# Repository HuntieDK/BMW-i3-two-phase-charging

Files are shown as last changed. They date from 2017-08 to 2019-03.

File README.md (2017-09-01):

# BMW i3 60Ah two-phase charging

This repository contains schematics, PCB layout and Arduino IDE compatible
code for extending the BMW i3 60Ah BEV/REX charging to use two phases
for charging through the type 2 receptable in the car.

## Background

The BMW i3 60Ah is designed to charge with 230V/32A (7.4kW) from a single
phase supply. However often a three-phase 230V/16A supply is available
which can supply 11kW, but this only lets the i3 charge with 230V/16A (3.7kW),
as the i3 can only use one of the phases.

Internally in the car, the 32A current is split between two charging units,
the EME and the KLE. These actually pull up to 16A each, and can, with
modification, be made to charge from two individual phases. In this way,
the car can charge from two phases, 230V at 16A each, in total 7.4kW.

## Implementation

* The wiring in the car must be changed. A new three-phase socket must be
  installed and new wiring must be pulled from the replaced socket to the
  KLE and EME units

* The car must be persuaded to pull what it believes is 32A in order to
  pull 16A on each phase. That is accomplished by the electronics and
  firmware in this repository. It must be inserted in the proximity and
  control pilot signals between the car's charging socket and the charging
  controller, LIM. The main function of the circuit is to signal "32A" over
  the control pilot line whenever the connected EVSE signals "16A" or more.

## Warning

This modification of the BMW i3 60Ah IS NOT SIMPLE! It requires electrical,
mecanical and electronical skills to complete the modification succesfully
in a safe way. The information here is provided "as is" without warranty of
any kind. See attached license.

ANY WORK YOU PERFORM BASED ON THIS DESCRIPTION IS YOUR OWN RESPONSIBILITY!

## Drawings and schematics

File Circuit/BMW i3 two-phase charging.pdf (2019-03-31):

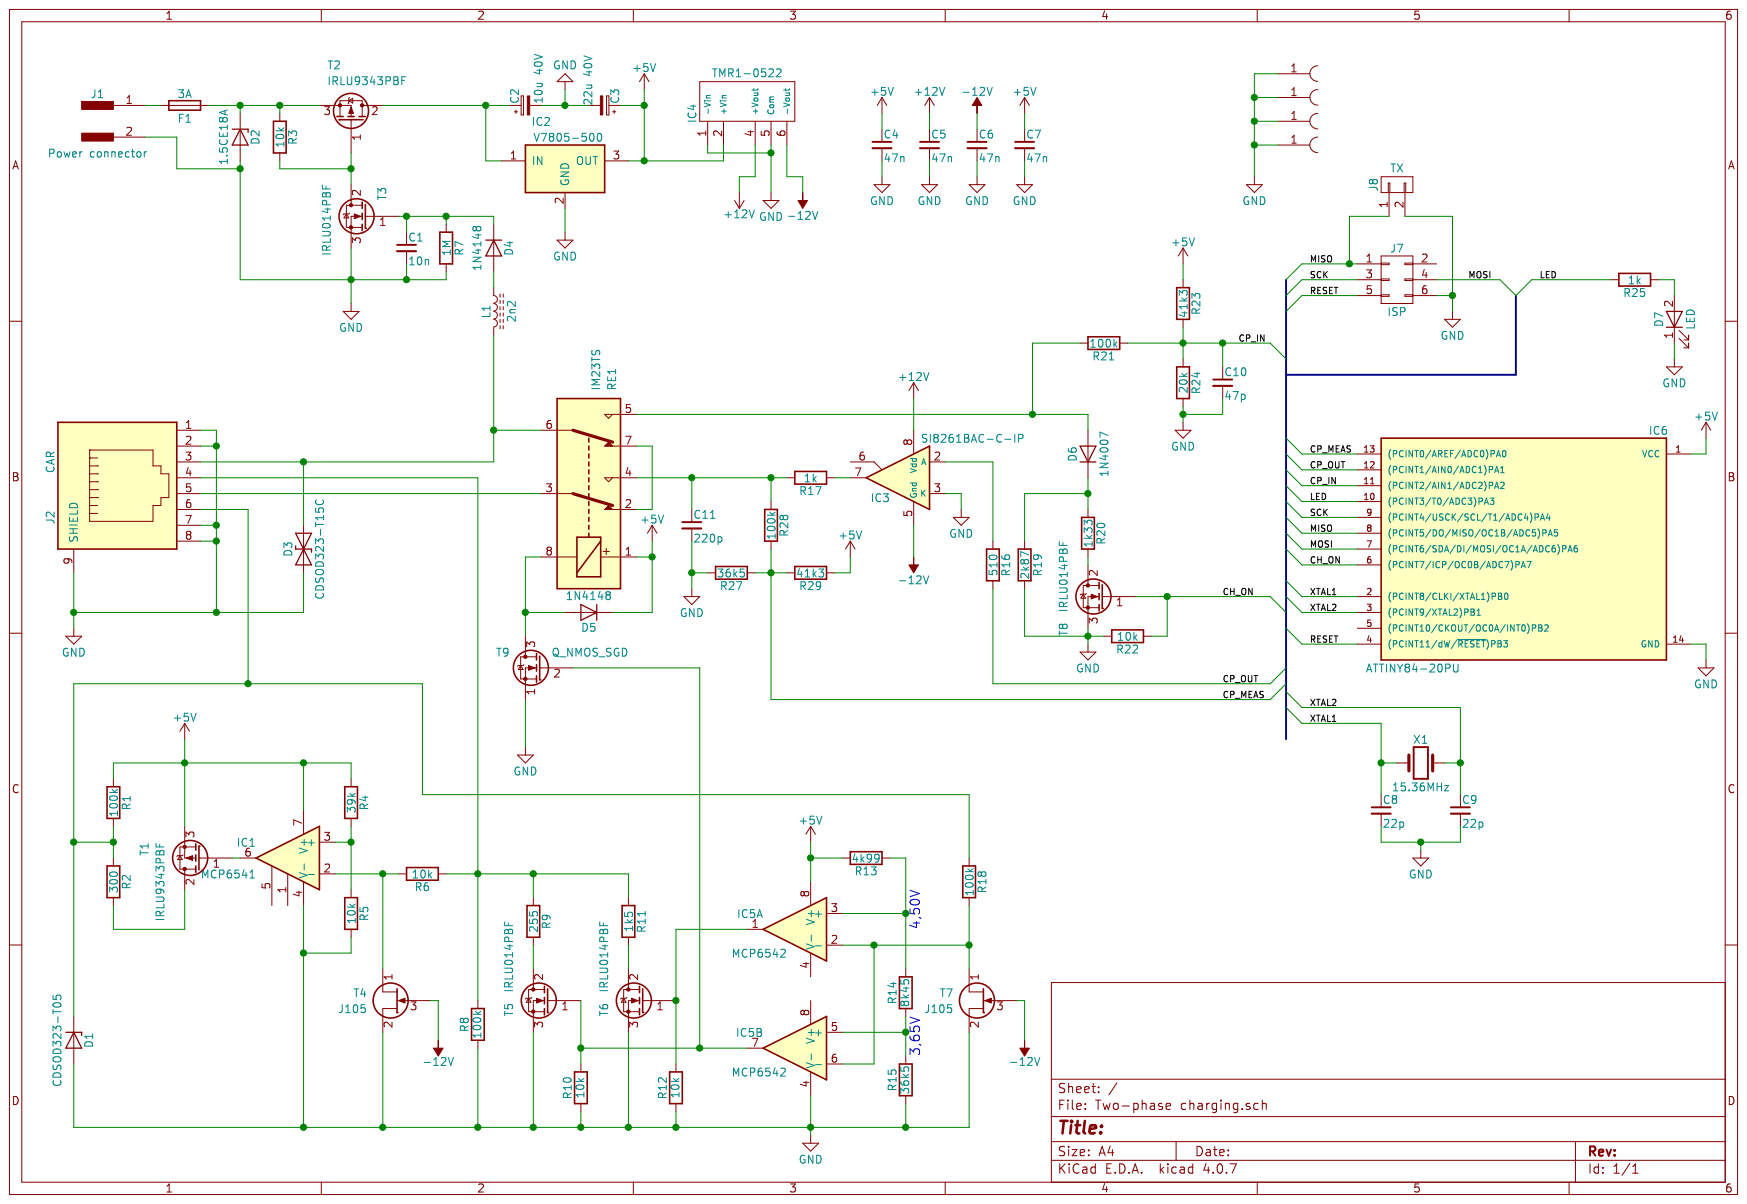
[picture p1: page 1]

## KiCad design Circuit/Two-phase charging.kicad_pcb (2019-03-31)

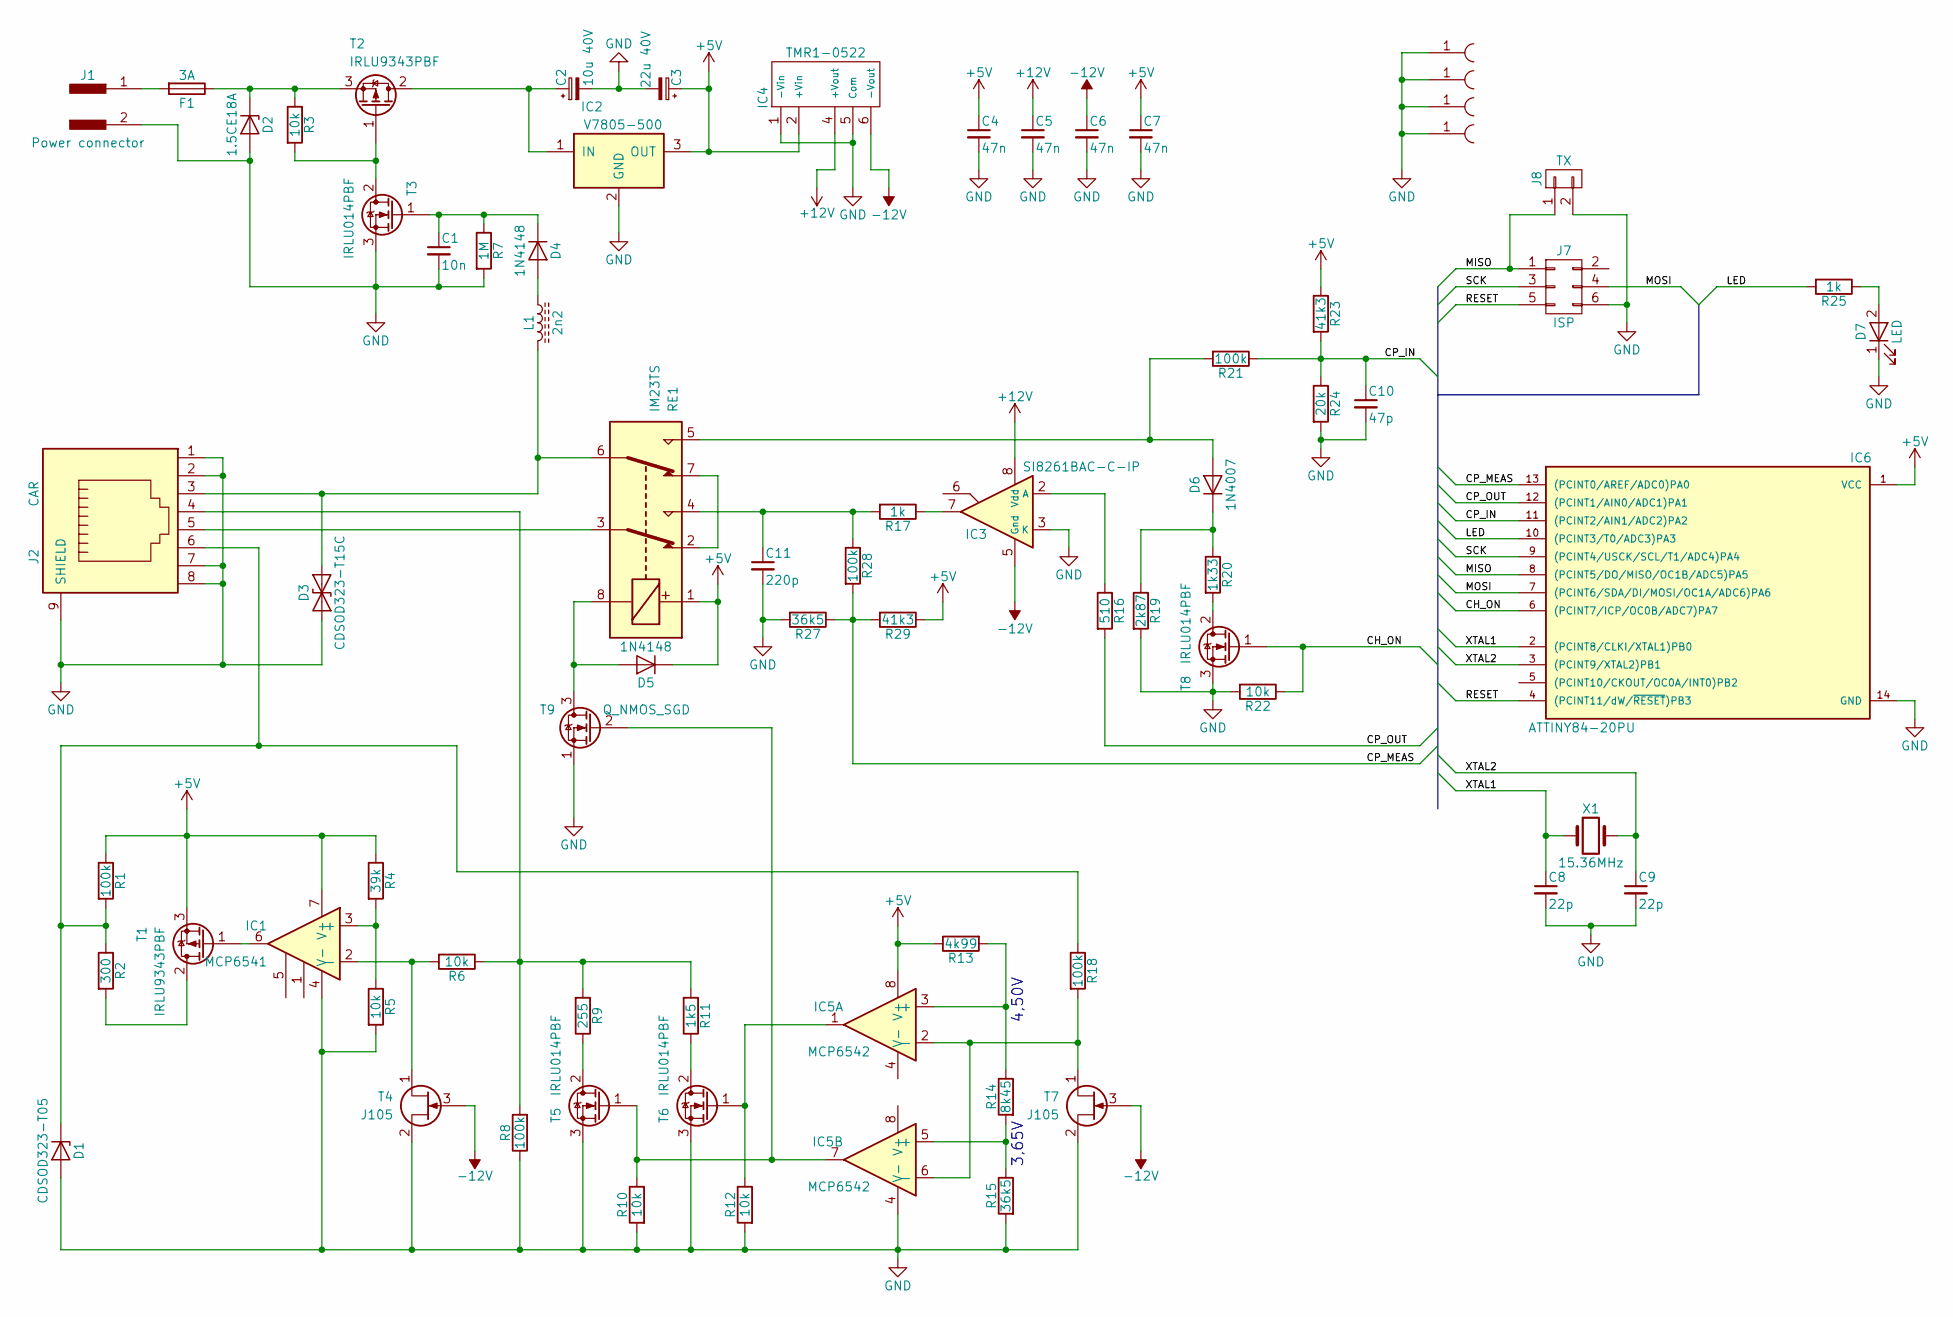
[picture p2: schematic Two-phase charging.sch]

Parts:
C1: 10n; C_Disc_D5.1mm_W3.2mm_P5.08mm
C2: 10u 40V; CP_Radial_D5.0mm_P2.50mm
C3: 22u 40V; CP_Radial_D5.0mm_P2.50mm
C4, C5, C6, C7: 47n; C_Disc_D5.1mm_W3.2mm_P5.08mm
C8, C9: 22p; Pin_Header_Straight_1x02_Pitch2.54mm
C10: 47p; Pin_Header_Straight_1x02_Pitch2.54mm
C11: 220p; Pin_Header_Straight_1x02_Pitch2.54mm
D1: CDSOD323-T05; D_SOD-323_HandSoldering
D2: 1.5CE18A; D_DO-201AD_P12.70mm_Horizontal
D3: CDSOD323-T15C; D_SOD-323_HandSoldering
D4, D5: 1N4148; D_DO-41_SOD81_P7.62mm_Horizontal
D6: 1N4007; D_DO-41_SOD81_P10.16mm_Horizontal
D7: LED; LED_D3.0mm
F1: 3A; R_Axial_DIN0207_L6.3mm_D2.5mm_P10.16mm_Horizontal
IC1: MCP6541; DIP-8_W7.62mm_LongPads
IC2: V7805-500; VX78xx-500
IC3: SI8261BAC-C-IP; DIP-8_W7.62mm_LongPads
IC4: TMR1-0522; Recom_1x05_Pitch2.54mm
IC5: MCP6542; DIP-8_W7.62mm_LongPads
IC6: ATTINY84-20PU; DIP-14_W7.62mm_LongPads
J1: Power connector; PINHEAD1-2
J2: CAR; RJ45_8_TM21R
J3, J4, J5, J6: Mount; MountingHole_3.5mm_Pad
J7: ISP; Pin_Header_Straight_2x03_Pitch2.54mm
J8: TX; Pin_Header_Straight_1x02_Pitch2.54mm
L1: 2n2; L_Axial_L11.0mm_D4.5mm_P5.08mm_Vertical_Fastron_MECC
R1, R8, R18, R21, R28: 100k; R_Axial_DIN0207_L6.3mm_D2.5mm_P10.16mm_Horizontal
R2: 300; R_Axial_DIN0207_L6.3mm_D2.5mm_P10.16mm_Horizontal
R3, R5, R6, R10, R12, R22: 10k; R_Axial_DIN0207_L6.3mm_D2.5mm_P10.16mm_Horizontal
R4: 39k; R_Axial_DIN0207_L6.3mm_D2.5mm_P10.16mm_Horizontal
R7: 1M; R_Axial_DIN0207_L6.3mm_D2.5mm_P10.16mm_Horizontal
R9: 255; R_Axial_DIN0207_L6.3mm_D2.5mm_P10.16mm_Horizontal
R11: 1k5; R_Axial_DIN0207_L6.3mm_D2.5mm_P10.16mm_Horizontal
R13: 4k99; R_Axial_DIN0207_L6.3mm_D2.5mm_P10.16mm_Horizontal
R14: 8k45; R_Axial_DIN0207_L6.3mm_D2.5mm_P10.16mm_Horizontal
R15, R27: 36k5; R_Axial_DIN0207_L6.3mm_D2.5mm_P10.16mm_Horizontal
R16: 510; R_Axial_DIN0207_L6.3mm_D2.5mm_P10.16mm_Horizontal
R17, R25: 1k; R_Axial_DIN0207_L6.3mm_D2.5mm_P10.16mm_Horizontal
R19: 2k87; R_Axial_DIN0207_L6.3mm_D2.5mm_P10.16mm_Horizontal
R20: 1k33; R_Axial_DIN0207_L6.3mm_D2.5mm_P10.16mm_Horizontal
R23, R29: 41k3; R_Axial_DIN0207_L6.3mm_D2.5mm_P10.16mm_Horizontal
R24: 20k; R_Axial_DIN0207_L6.3mm_D2.5mm_P10.16mm_Horizontal
RE1: IM23TS; Relay_DPDT_AXICOM_IMSeries_Pitch5.08mm
T1, T2: IRLU9343PBF; TO-251_IPAK_Vertical
T3, T5, T6, T8: IRLU014PBF; TO-251_IPAK_Vertical
T4, T7: J105; TO-92_Molded_Wide
T9: Q_NMOS_SGD; TO-92_Molded_Wide
X1: 15.36MHz; Crystal_HC49-U_Vertical

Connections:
+5V: C3.1, C4.1, C7.1, D5.1 (K), IC1.7 (V+), IC2.3 (OUT), IC4.2 (+Vin), IC5.8 (V+), IC6.1 (VCC), R1.1, R4.1, R13.1, R23.1, R29.1, RE1.1, T1.3 (S)
+12V: C5.1, IC3.8 (Vdd), IC4.4 (+Vout)
-12V: C6.1, IC3.5 (Gnd), IC4.6 (-Vout), T4.3 (G), T7.3 (G)
/CH_ON: IC6.6 ((PCINT7/ICP/OC0B/ADC7)PA7), R22.1, T8.1 (G)
/CP_IN: C10.1, IC6.11 ((PCINT2/AIN1/ADC2)PA2), R21.1, R23.2, R24.1
/CP_MEAS: IC6.13 ((PCINT0/AREF/ADC0)PA0), R27.1, R28.2, R29.2
/CP_OUT: IC6.12 ((PCINT1/AIN0/ADC1)PA1), R16.2
/LED: IC6.10 ((PCINT3/T0/ADC3)PA3), R25.2
/MISO: IC6.8 ((PCINT5/DO/MISO/OC1B/ADC5)PA5), J7.1, J8.1
/MOSI: IC6.7 ((PCINT6/SDA/DI/MOSI/OC1A/ADC6)PA6), J7.4
/RESET: IC6.4 ((PCINT11/dW/~RESET~)PB3), J7.5
/SCK: IC6.9 ((PCINT4/USCK/SCL/T1/ADC4)PA4), J7.3
/XTAL1: C8.1, IC6.2 ((PCINT8/CLKI/XTAL1)PB0), X1.1
/XTAL2: C9.1, IC6.3 ((PCINT9/XTAL2)PB1), X1.2
GND: C1.2, C2.2, C3.2, C4.2, C5.2, C6.2, C7.2, C8.2, C9.2, C10.2, C11.2, D1.2 (A), D2.2 (A), D3.1 (A1), D7.1 (K), IC1.4 (V-), IC2.2 (GND), IC3.3 (K), IC4.1 (-Vin), IC4.5 (Com), IC5.4 (V-), IC6.14 (GND), J1.2, J2.1, J2.2, J2.7, J2.8, J2.9 (SHIELD), J3.1, J4.1, J5.1, J6.1, J7.6, J8.2, R5.2, R7.2, R8.1, R10.2, R12.2, R15.2, R19.2, R22.2, R24.2, R27.2, T3.3 (S), T4.2 (S), T5.3 (S), T6.3 (S), T7.2 (S), T8.3 (S), T9.1 (S)
unnamed: C1.1, D4.1 (K), R7.1, T3.1 (G)
unnamed: C2.1, IC2.1 (IN), T2.2 (D)
unnamed: C11.1, R17.2, R28.1, RE1.4
unnamed: D1.1 (K), J2.6, R1.2, R2.1, R18.1
unnamed: D2.1 (K), F1.1, R3.1, T2.3 (S)
unnamed: D3.2 (A2), J2.3, L1.2, RE1.6
unnamed: D4.2 (A), L1.1
unnamed: D5.2 (A), RE1.8, T9.3 (D)
unnamed: D6.1 (K), R19.1, R20.1
unnamed: D6.2 (A), R21.2, RE1.5
unnamed: D7.2 (A), R25.1
unnamed: F1.2, J1.1
unnamed: IC1.2 (-), R6.2, T4.1 (D)
unnamed: IC1.3 (+), R4.2, R5.1
unnamed: IC1.6, T1.1 (G)
unnamed: IC3.2 (A), R16.1
unnamed: IC3.7, R17.1
unnamed: IC5.1, R12.1, T6.1 (G)
unnamed: IC5.2 (-), IC5.6 (-), R18.2, T7.1 (D)
unnamed: IC5.3 (+), R13.2, R14.1
unnamed: IC5.5 (+), R14.2, R15.1
unnamed: IC5.7, R10.1, T5.1 (G), T9.2 (G)
unnamed: J2.4, R6.1, R8.2, R9.2, R11.2
unnamed: J2.5, RE1.3
unnamed: R2.2, T1.2 (D)
unnamed: R3.2, T2.1 (G), T3.2 (D)
unnamed: R9.1, T5.2 (D)
unnamed: R11.1, T6.2 (D)
unnamed: R20.2, T8.2 (D)
unnamed: RE1.2, RE1.7

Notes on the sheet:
3,65V
4,50V

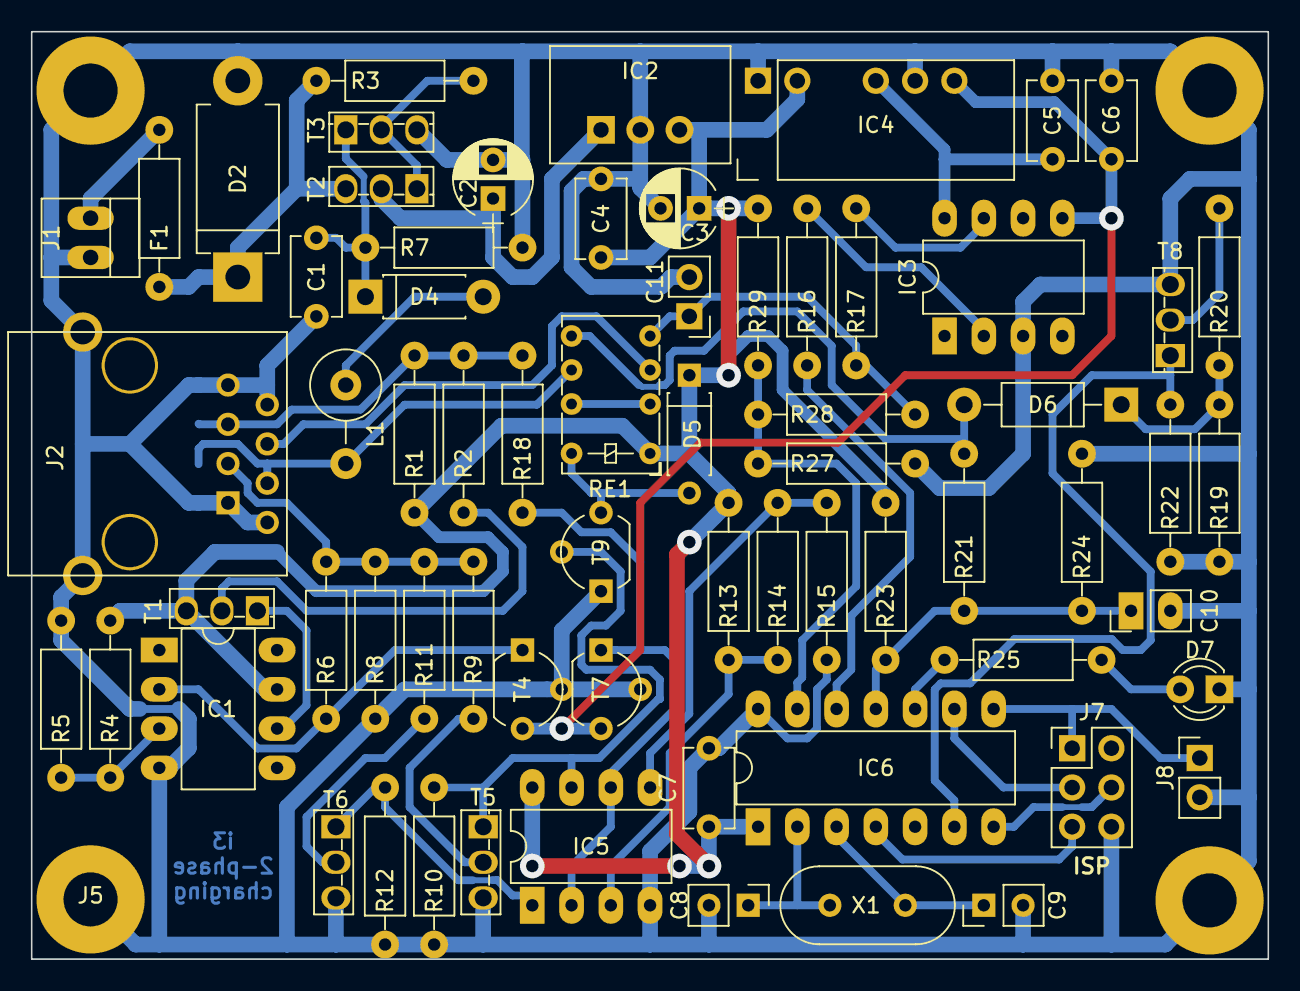
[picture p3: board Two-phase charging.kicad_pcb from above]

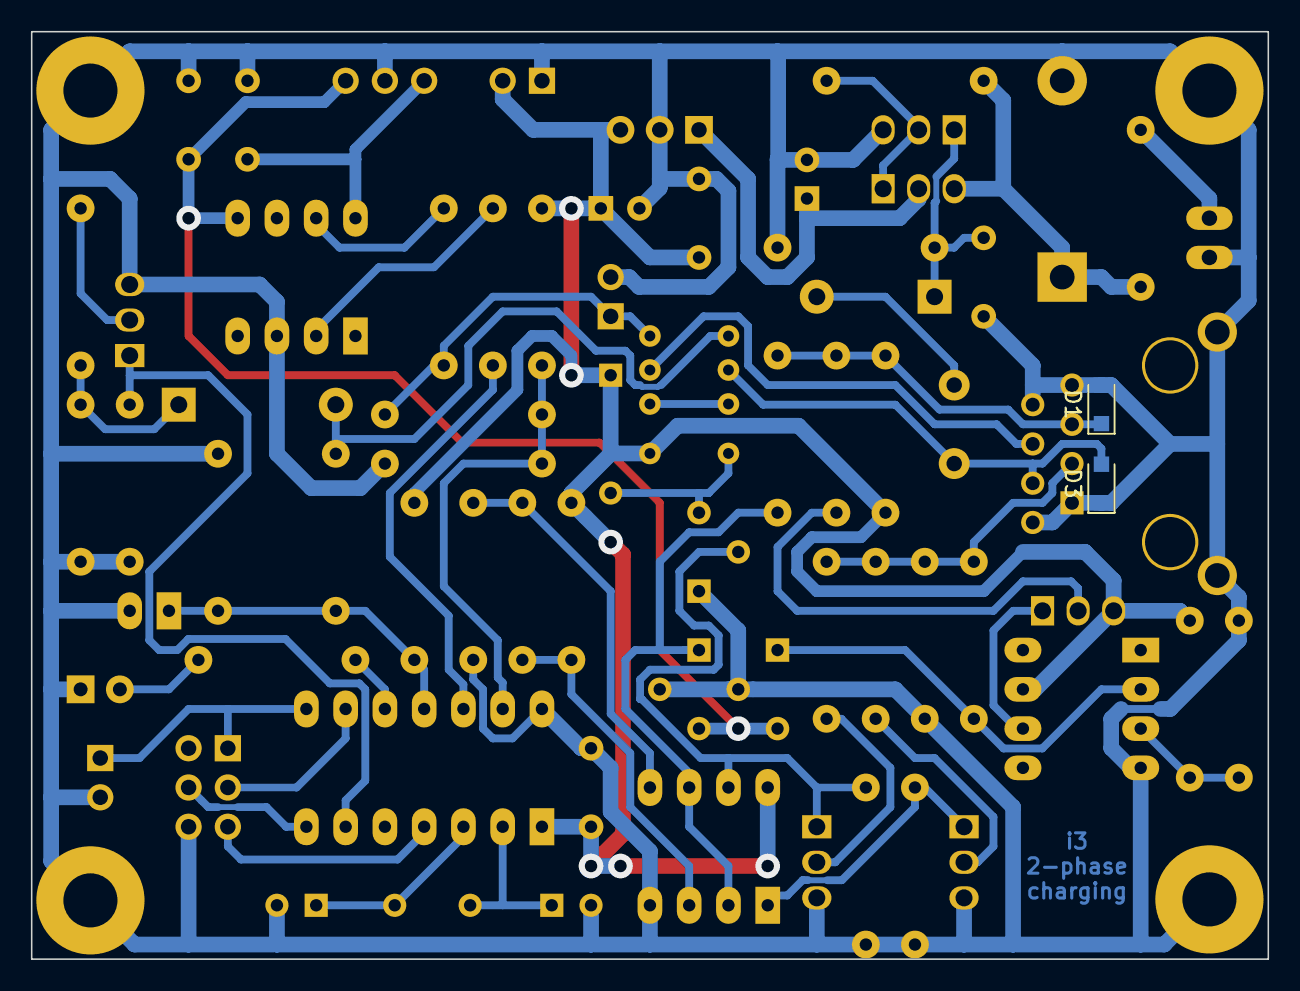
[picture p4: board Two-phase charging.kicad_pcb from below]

Board: 2 copper layers, 80.0 x 60.0 mm, 73 parts (2 on the bottom side), 45 nets.

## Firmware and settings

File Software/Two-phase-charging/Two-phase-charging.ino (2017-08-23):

// Sketch for Attiny84 handling two-phase charging extension in BMW i3

#include "USISerialSend.h"

#define PIN_CP_MEAS 0   // PA0 pin 13
#define PIN_CP_OUT  1   // PA2 pin 12
#define PIN_CP_IN   2   // PA2 pin 11
#define PIN_LED_OUT 3   // PA3 pin 10
#define PIN_CH_ON   7   // PA7 pin 6

#define AD_CP_MEAS  0   // ADC port to read CP voltage
#define AD_CP_IN    2   // ADC port to detect ingoing CP

// Our clock frequency is 15.36 MHz. 6A = 10% pwm so 1A = 10/6% of 10 us = 16 2/3 us.
// Our clock tick is 1/15.36 us, so clocks/amp = 16 2/3*15.36 = 256.

#define AMPCNT(current) (static_cast<unsigned int>(current) << 8)  // Multiply by 256
#define AMPCNT_HALF     (128)

#define MEASCNT         AMPCNT(3)     // Measurement at 5% of cycle after each change
#define EXTENDCNT       (AMPCNT(15))  // If 16A (actually >= 15.5A) indicated, double current.

#define WR_HL_WRAP(REGH, REGL, VAL) { REGH = ((VAL)>>8)&0xff; REGL = (VAL)&0xff; }
#define WR_HL(REG, VAL) WR_HL_WRAP(REG##H, REG##L, VAL)

#define RD_LH_WRAP(REGH, REGL, VAL) { register byte reg = REGL; VAL = (static_cast<word>(REGH) << 8) | reg; }
#define RD_LH(REG, VAL) RD_LH_WRAP(REG##H, REG##L, VAL)

#define STOP_TIMER    { TCCR1B = 0; }         // Counter stopped
#define START_TIMER   { STOP_TIMER; WR_HL(TCNT1, 0); TCCR1B = _BV(CS10); } // No prescaling i.e. 15.36MHz counting.

#define LEVEL_UNDEF     0
#define LEVEL_LOW12     1
#define LEVEL_HIGH3     2
#define LEVEL_HIGH6     3
#define LEVEL_HIGH9     4
#define LEVEL_HIGH12    5
#define N_LEVELS        6

static const byte levelMap[1023*3/100] /*PROGMEM*/ = {
  LEVEL_LOW12,  // -12 - -11
  LEVEL_UNDEF,  // -11 - -10
  LEVEL_UNDEF,  // -10 - -9
  LEVEL_UNDEF,  // -9  - -8
  LEVEL_UNDEF,  // -8  - -7
  LEVEL_UNDEF,  // -7  - -6
  LEVEL_UNDEF,  // -6  - -5
  LEVEL_UNDEF,  // -5  - -4
  LEVEL_UNDEF,  // -4  - -3
  LEVEL_UNDEF,  // -3  - -2
  LEVEL_UNDEF,  // -2  - -1
  LEVEL_UNDEF,  // -1  -  0
  LEVEL_UNDEF,  //  0  -  1
  LEVEL_UNDEF,  //  1  -  2
  LEVEL_HIGH3,  //  2  -  3
  LEVEL_HIGH3,  //  3  -  4
  LEVEL_UNDEF,  //  4  -  5
  LEVEL_HIGH6,  //  5  -  6
  LEVEL_HIGH6,  //  6  -  7
  LEVEL_UNDEF,  //  7  -  8
  LEVEL_HIGH9,  //  8  -  9
  LEVEL_HIGH9,  //  9  - 10
  LEVEL_UNDEF,  // 10  - 11
  LEVEL_HIGH12, // 11  - 12
  LEVEL_HIGH12, // 12  - 13
  LEVEL_UNDEF,  // 13  - 14
  LEVEL_UNDEF,  // 14  - 15
  LEVEL_UNDEF,  // 15  - 16
  LEVEL_UNDEF,  // 16  - 17
  LEVEL_UNDEF,  // 17  - 18
};

static bool cpIn = false; // Indicate last CP input (true = high)

static word upCnt = 0;  // Number of rising CP edges
static word dnCnt = 0;  // Number of falling CP edges

static bool extending = false;  // Currently extending PWM
static byte evseCurrent = 0;  // Number of ampere indicated by EVSE

static bool doing32A = false;  // True when extending to 32A

void setup() {
  // put your setup code here, to run once:

  // Init status led:
  pinMode(PIN_LED_OUT, OUTPUT);  // Status LED
  digitalWrite(PIN_LED_OUT, LOW);

  // Init other pins:
  pinMode(PIN_CP_OUT, OUTPUT);     // PWM output initially high
  digitalWrite(PIN_CP_OUT, HIGH);

  pinMode(PIN_CH_ON, OUTPUT);       // Charge indication to car initially off
  digitalWrite(PIN_CH_ON, LOW);
  
  word pilot = 0;
  
  analogReference(DEFAULT);       // 5V analog reference
  
  // Set up AD manually for car CP measurements as it must be interrupt controlled:
  ADCSRA = _BV(ADEN)|_BV(ADIE)|_BV(ADPS2);  // Enable ADC, ADC interrupts, clock divisor 16
  ADCSRB = 0;
  ADMUX = AD_CP_MEAS;
  DIDR0 |= _BV(AD_CP_MEAS);  // Disable digital input on A0

  // Set up timer 1 for duty-cycle measurement and AD start interrupt
  TCCR1A  = 0;
  TCCR1B  = 0; // Prescaler disabled so timer is stopped
  TCCR1C  = 0;
  TIMSK1  = _BV(OCIE1A)|_BV(OCIE1B)|_BV(TOIE1);  // Interrupt on match OCR1A: 5% passed; measure CP voltage; interrupt on match OCR1B: Max PWM reached and on full run (line stuck)
  TIFR1   = 0;
  WR_HL(OCR1A, MEASCNT);      // First interrupt at measurement PWM
  WR_HL(OCR1B, EXTENDCNT);    // Second interrupt at PWM wide enough for us to expand to 32A
  WR_HL(ICR1, 0);
  WR_HL(TCNT1, 0);  // Initialize timer value

  // Initialize comparator
  ADCSRB  &=  ~_BV(ACME);           // Clear ACME flag to prepare for bandgap as reference
  ACSR    =   _BV(ACBG)|_BV(ACIE);  // (Enable), use bandgap, enable interrupts, (interrupt on toggle)
  DIDR0   |= _BV(AD_CP_IN);  // Disable digital input on A0

  // We're running; most stuff will run in interrupt routines.
  serialSetup();
  serialWrite("BMW i3 two phase charging running\n\r");
}

ISR(ANA_COMP_vect)  // Control pilot toggled.
{
  cpIn = (ACSR & _BV(ACO)) == 0;    // Current CP state from EVSE

  if (cpIn) {
    digitalWrite(PIN_CP_OUT, HIGH); // Output CP high
    upCnt++;  // We got a leading CP edge.
    WR_HL(OCR1B, EXTENDCNT);   // Interrupt at time ready for extending to 32A
    extending = false;  // not yet extending
    START_TIMER;  // Start the timer so we will make the relevant measurements.*/
  } else {
    if (!extending) {
      digitalWrite(PIN_CP_OUT, LOW); // Output CP low as we're not extending to 32A at the moment.
    }
    dnCnt++;
    // Read timer value to get high PWM %
    register word cnt;
    RD_LH(TCNT1, cnt);
    evseCurrent = (cnt+AMPCNT_HALF) >> 8;
    doing32A = cnt >= EXTENDCNT;
    if (!extending) {
      START_TIMER;  // Start timer for negative cycle measurement
    } // Else: Wait for extending done
  }
}

ISR(TIMER1_COMPA_vect)  // Timer compare interrupt - start AD
{
  ADCSRA |= _BV(ADSC); // Start conversion
  if (!cpIn) {
    STOP_TIMER;  // No need for timer interrupts during negative cycle
  }
}

ISR(TIMER1_COMPB_vect)  // Timer reached 15.5A or 32A marks
{
  if (!extending) {
    if (cpIn) {
      // CP signal is still active - extend to 32A
      WR_HL(OCR1B, AMPCNT(32));  // Call this routine again at 32A mark
      extending = true;
    } else {
      // CP signal not active any more - stop timer. Actually we should never get here as timer is reset at AD point in negative cycle.
      STOP_TIMER;
    }
  } else {
    // We are extending and reached 32A mark - stop extending and stop timer
    digitalWrite(PIN_CP_OUT, LOW);  // Stop overriding PWM
    extending = false;
    START_TIMER;  // Start timer for negative cycle measurement
  }
}

// CP measurement:
static byte portLevel[2] = { LEVEL_HIGH12, LEVEL_HIGH12 };
static volatile bool chargeOn = false;

static uint16_t measureLevel[2] = {0,0};

ISR(ADC_vect)
{
  uint16_t level;
  RD_LH(ADC, level);
  sei();
  measureLevel[cpIn] = level;
  portLevel[cpIn] = levelMap[level * 3 / 100];
  
  chargeOn = portLevel[false] == LEVEL_LOW12 && (portLevel[true] == LEVEL_HIGH6 || portLevel[true] == LEVEL_HIGH3);
  digitalWrite(PIN_CH_ON, chargeOn ? HIGH : LOW);
}

// No need for timer overflow for now: ISR(TIMER1_OVF_vect)  {}

static bool prevChargeOn = false;
static bool prev32A = false;
static bool prevDC = false;
static byte prevCurrent = 0;

char s[16];

static const char* on = "ON\r\n";
static const char* off = "OFF\r\n";

void loop()
{
  bool dc = (evseCurrent >= 2 && evseCurrent <= 4);
  register byte act = chargeOn ? LOW : HIGH;
  register byte inAct = chargeOn ? HIGH : LOW;
  digitalWrite(PIN_LED_OUT, inAct);
  serialDelay(1200);
  digitalWrite(PIN_LED_OUT, (doing32A) ? act : inAct);
  serialDelay(200);
  digitalWrite(PIN_LED_OUT, inAct);
  serialDelay(200);
  digitalWrite(PIN_LED_OUT, act);
  serialDelay(200);

  if (chargeOn != prevChargeOn) {
    serialWrite("Charging: ");
    serialWrite(chargeOn ? on : off);
    prevChargeOn = chargeOn;
  }

  if (doing32A != prev32A) {
    serialWrite("32A extending: ");
    serialWrite(doing32A ? on : off);
    prev32A = doing32A;
  }

  if (prevDC != dc) {
    serialWrite("DC charger: ");
    serialWrite(dc ? on : off);
    prevDC = dc;
  }

  if (prevCurrent != evseCurrent) {
    serialWrite("EVSE current: ");
    sprintf(s, "%d", evseCurrent);
    serialWrite(s);
    serialWrite("\r\n");
    prevCurrent = evseCurrent;
  }
  
  /*serialWrite("Upcount: ");
  sprintf(s, "%d\r\n", upCnt);
  serialWrite(s);
  serialWrite("Downcount: ");
  sprintf(s, "%d\r\n", dnCnt);
  serialWrite(s);

  serialWrite("Level[0]: ");
  sprintf(s, "%d\r\n", portLevel[false]);
  serialWrite(s);
  serialWrite("Level[1]: ");
  sprintf(s, "%d\r\n", portLevel[true]);
  serialWrite(s);*/
}

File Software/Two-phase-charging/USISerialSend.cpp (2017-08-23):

#include <Arduino.h>
#include "USISerialSend.h"
/*  
 An example of USI Serial Send for ATtiny24/44/84.
 Sends a text message every second.
   
ATTiny84 PA5/MISO/DO = Serial UART Tx -> connect to Rx of serial output device
*/

/* Supported combinations:
 *   F_CPU 1000000   BAUDRATE 1200, 2400 
 *   F_CPU 8000000   BAUDRATE 9600, 19200
 *   F_CPU 16000000  BAUDRATE 9600, 19200, 28800, 38400
 */

// Set your baud rate and number of stop bits here
#define BAUDRATE            2400
#define STOPBITS            1
#define F_CPU 15360000  // Our cpu runs at 15.36 MHz

// If bit width in cpu cycles is greater than 255 then divide by 8 to fit in timer
// Calculate prescaler setting
#define CYCLES_PER_BIT       ( (F_CPU) / (BAUDRATE) )
#if (CYCLES_PER_BIT >= 256)
  #if (CYCLES_PER_BIT >= 2048)
    #define DIVISOR             64
    #define CLOCKSELECT         3
  #else
    #define DIVISOR             8
    #define CLOCKSELECT         2
  #endif
#else
  #define DIVISOR             1
  #define CLOCKSELECT         1
#endif
#define FULL_BIT_TICKS      ( (CYCLES_PER_BIT) / (DIVISOR) )

// Old timer values
#ifdef ARDUINO
volatile static uint8_t oldTCCR0A;
volatile static uint8_t oldTCCR0B;
volatile static uint8_t oldTCNT0;
#endif

// USISerial send state variable and accessors
enum USISERIAL_SEND_STATE { AVAILABLE, FIRST, SECOND };
static volatile enum USISERIAL_SEND_STATE usiserial_send_state = AVAILABLE;

static inline enum USISERIAL_SEND_STATE usiserial_send_get_state(void)
{
    return usiserial_send_state;
}

static inline void usiserial_send_set_state(enum USISERIAL_SEND_STATE state)
{
    usiserial_send_state=state;
}

bool usiserial_send_available()
{
    return usiserial_send_get_state()==AVAILABLE;
}

// Transmit data persistent between USI OVF interrupts
static volatile uint8_t usiserial_tx_data;

static inline uint8_t usiserial_get_tx_data(void)
{
    return usiserial_tx_data;
}

static inline void usiserial_set_tx_data(uint8_t tx_data)
{
    usiserial_tx_data = tx_data;
}

static uint8_t reverse_byte (uint8_t x) {
    x = ((x >> 1) & 0x55) | ((x << 1) & 0xaa);
    x = ((x >> 2) & 0x33) | ((x << 2) & 0xcc);
    x = ((x >> 4) & 0x0f) | ((x << 4) & 0xf0);
    return x;
}

void usiserial_send_byte(uint8_t data)
{
    while (usiserial_send_get_state() != AVAILABLE)
    {
        // Spin until we finish sending previous packet
    };
    usiserial_send_set_state(FIRST);
    usiserial_set_tx_data(reverse_byte(data));

    // Configure Timer0
    TCCR0A = 2<<WGM00;                      // CTC mode
    TCCR0B = CLOCKSELECT;                   // Set prescaler to clk or clk /8
    GTCCR |= _BV(PSR10);                    // Reset prescaler
    OCR0A = FULL_BIT_TICKS;                 // Trigger every full bit width
    TCNT0 = 0;                              // Count up from 0 
    TIMSK0 |= 1<<OCIE0A;                    // Interrupt on match for our simple timer

    // Configure USI to send high start bit and 7 bits of data
    USIDR = 0x00 |                            // Start bit (low)
        usiserial_get_tx_data() >> 1;         // followed by first 7 bits of serial data
    USICR  = (1<<USIOIE)|                     // Enable USI Counter OVF interrupt.
        (0<<USIWM1)|(1<<USIWM0)|              // Select three wire mode to ensure USI written to PB1
        (0<<USICS1)|(1<<USICS0)|(0<<USICLK);  // Select Timer0 Compare match as USI Clock source.
    DDRA  |= (1<<PA5);                        // Configure USI_DO as output.
    USISR = 1<<USIOIF |                       // Clear USI overflow interrupt flag
        (16 - 8);                             // and set USI counter to count 8 bits
}

// USI overflow interrupt indicates we have sent a buffer
ISR (USI_OVF_vect)
{
    if (usiserial_send_get_state() == FIRST)
    {
        usiserial_send_set_state(SECOND);
        USIDR = usiserial_get_tx_data() << 7  // Send last 1 bit of data
            | 0x7F;                           // and stop bits (high)
        USISR = 1<<USIOIF |                   // Clear USI overflow interrupt flag
            (16 - (1 + (STOPBITS)));          // Set USI counter to send last data bit and stop bits
    }
    else
    {
        PORTB |= 1 << PB1;                    // Ensure output is high
        DDRB  |= (1<<PB1);                    // Configure USI_DO as output.
        USICR = 0;                            // Disable USI.
        USISR |= 1<<USIOIF;                   // clear interrupt flag

        usiserial_send_set_state(AVAILABLE);
    }
}

void serialSetup() {
    pinMode(5,HIGH);                // Configure USI_DO as output.
    digitalWrite(5,HIGH);           // Ensure serial output is high when idle
}

void serialWrite(const char* str)
{
  for (; *str; ++str) {
    while (!usiserial_send_available());
    usiserial_send_byte(*str);
  }
  while (!usiserial_send_available());
}

static volatile uint16_t timerCnt = 0;

ISR(TIMER0_COMPA_vect)  // Every time we pass 
{
  timerCnt++;
}

void serialDelay(uint16_t cnt)
{
  uint16_t start = timerCnt;
  while (timerCnt-start < cnt);
}

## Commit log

2017-08-23 Added schematics and PCB layout
2017-08-23 Added schematics and PCB
    [Two-phase charging.kicad_pcb, Two-phase charging.sch]
2017-08-23 Added arduino source for ATTINY84
2017-11-17 Added schematics as PDF
2019-03-31 Some PCB layout improvements
    [Two-phase charging.kicad_pcb]
